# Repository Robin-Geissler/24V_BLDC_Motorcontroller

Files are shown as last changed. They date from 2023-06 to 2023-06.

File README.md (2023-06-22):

# 24V BLDC Motorcontroller

This is a motorcontroller to control a 24V BLDC motor. In this project the controller was used to control a Faulhaber 4221 BXT R to power a 2DOF robot. The 6 Step control algorithm is used to control the motor. The motorcontroller implements the following control modes:
* Current Control
* Speed Control
* Position Control
* Torque Control

## Control Structure
A current controller and a speed controller are used as low level controllers for the position and torque controller. Each controlmode can be accessed by the user.

**Current Control** 
Uses currentsensors on the PCB to control the motor current. 

**Speed Control** 
Calculates the speed by analysing the HAL Sector change rate. 

**Position Control**
The position of the geaboxshaft is measured with an AksIM-2 absolute encoder from RLS. The control structure of the position controller looks like this:
grafik

**Torque Control**
The torque applied to the gearbox shaft is measured with a TS70a torque sensor from ME-Meßsysteme. The control structure of the torque controller looks like this:
grafik

## Comunication Interface
The controller provides an EtherCAT communication interface. Over the interface the controlmode can be set, and PID controlparameters for each controller can be manipulated.

## Hardware
A Microchip ATSAMD51G19A is used as an MCU. It controls a MP6540HA motordriver IC.
grafik

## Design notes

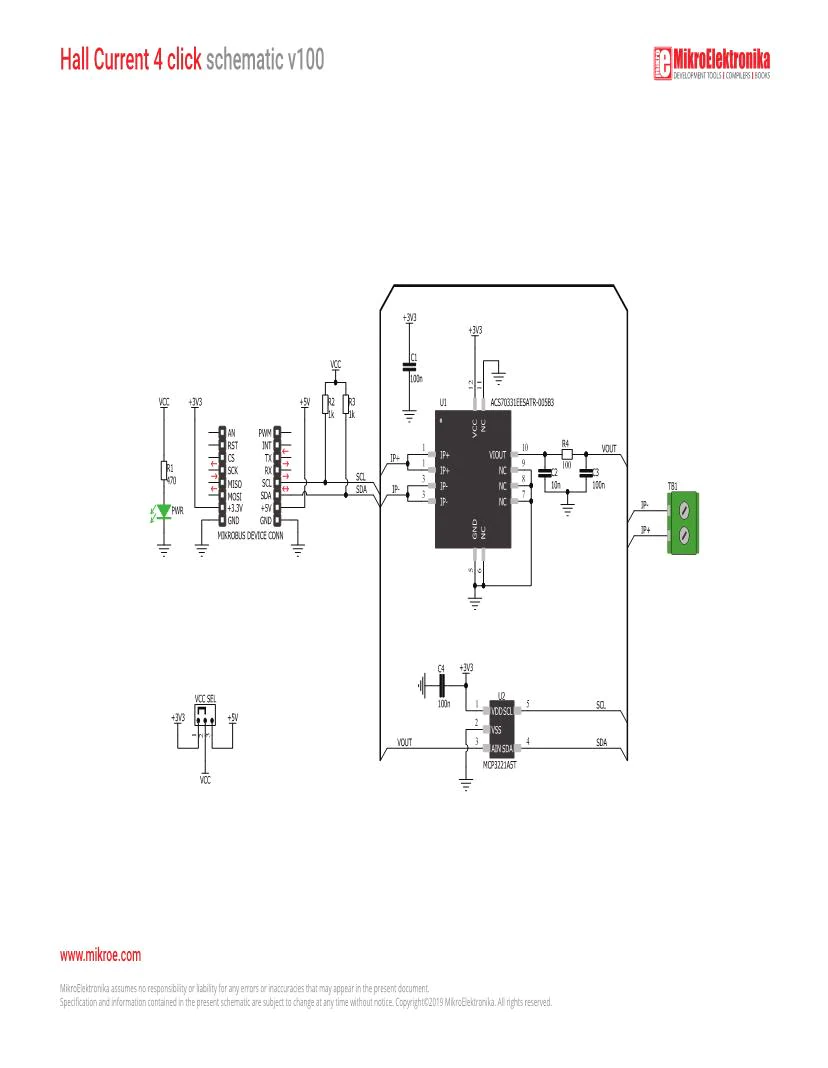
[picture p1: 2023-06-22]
PCB/hall-current-4-click-schematic-v100n-1864020.webp

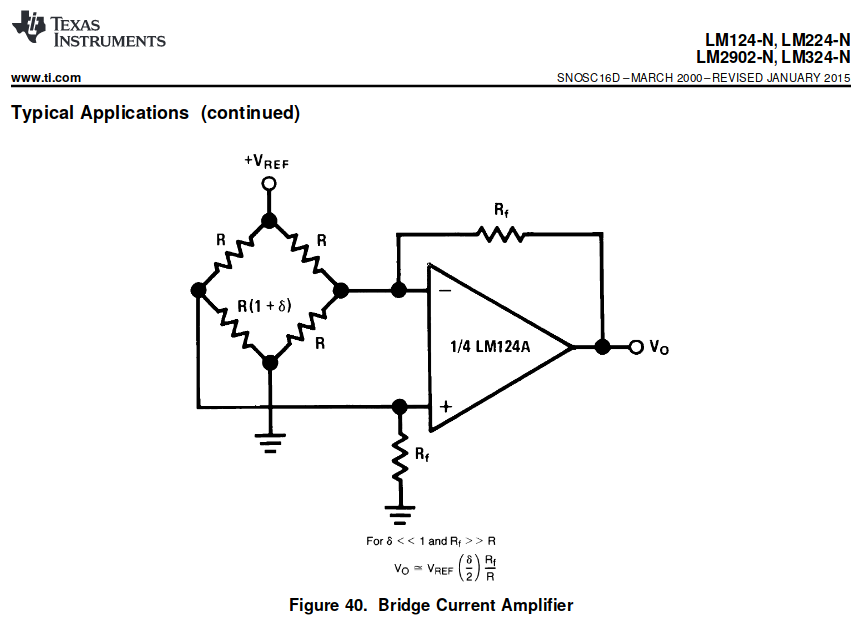
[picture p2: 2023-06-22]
PCB/PZ9ax.png

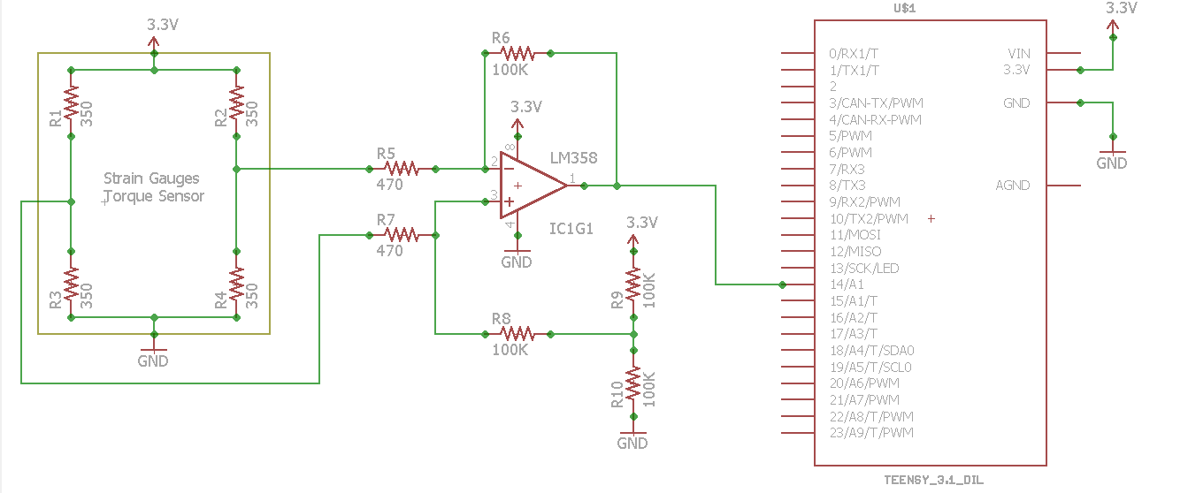
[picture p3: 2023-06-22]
PCB/torquesneosr1.webp

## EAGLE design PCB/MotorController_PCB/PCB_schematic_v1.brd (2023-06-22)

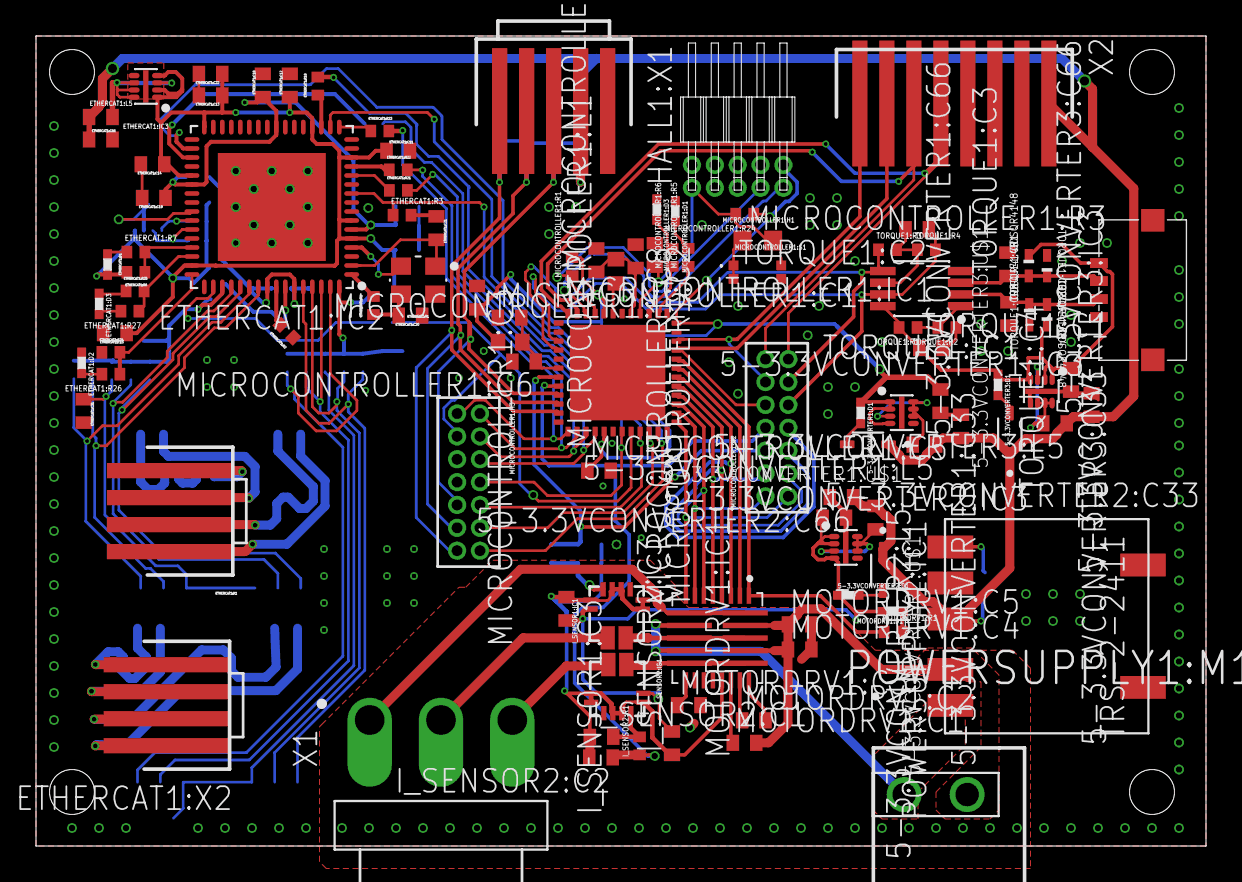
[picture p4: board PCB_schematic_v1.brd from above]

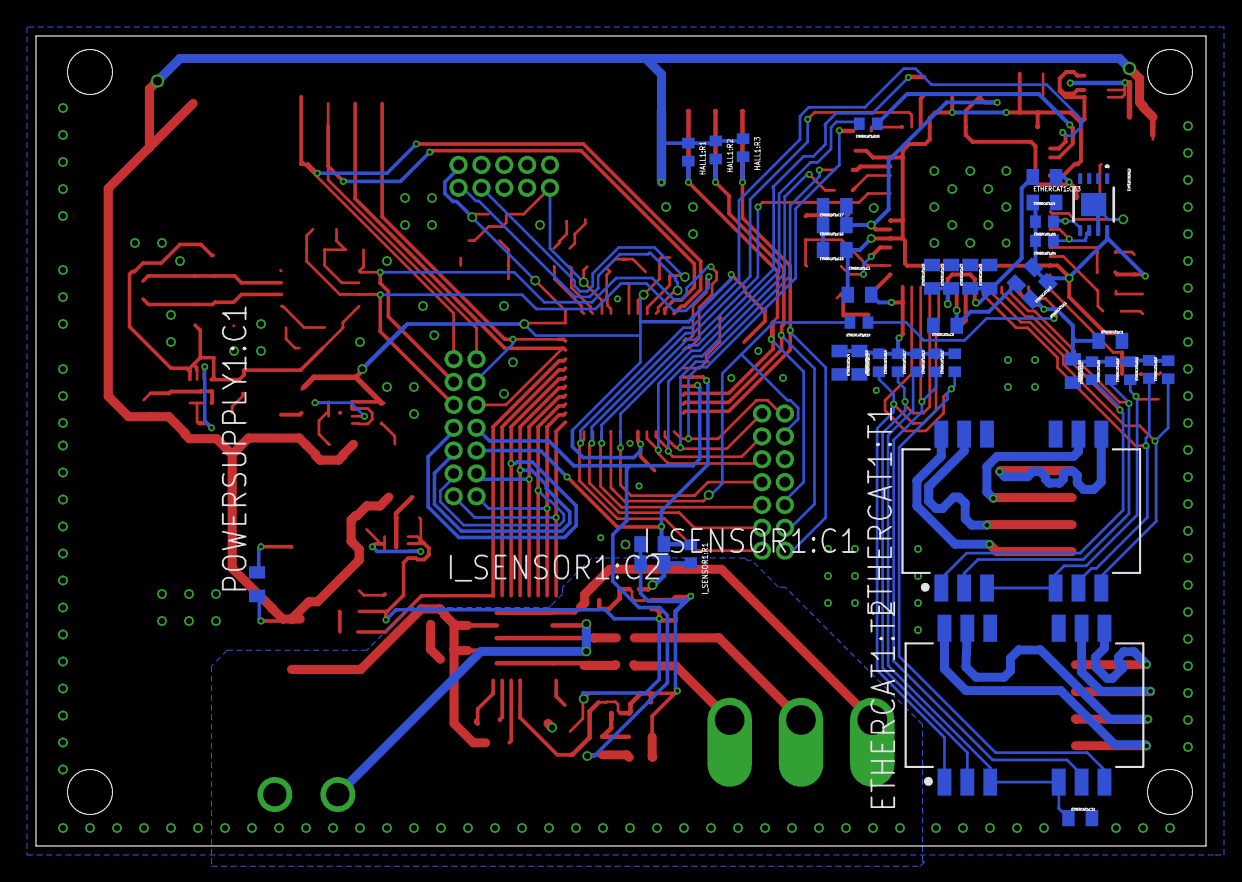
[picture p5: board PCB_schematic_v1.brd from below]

Board: 2 copper layers, 65.0 x 45.0 mm, 150 parts (42 on the bottom side), 111 nets.

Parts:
5-3.3VCONVERTER1:C33, 5-3.3VCONVERTER2:C33, 5-3.3VCONVERTER3:C33: GRM155C80J106ME11D; C0402
5-3.3VCONVERTER1:C66, 5-3.3VCONVERTER2:C66, 5-3.3VCONVERTER3:C66: GCM155C71A105KE38D; C0402
5-3.3VCONVERTER1:D1, 5-3.3VCONVERTER2:D1, 5-3.3VCONVERTER3:D1: QBLP595-R; LED0402
5-3.3VCONVERTER1:IC3, 5-3.3VCONVERTER2:IC3, 5-3.3VCONVERTER3:IC3: RP115L331D-E2; SON40P120X160X40-9T30X130N
5-3.3VCONVERTER1:L5, 5-3.3VCONVERTER2:L5, 5-3.3VCONVERTER3:L5: BLM15EG221SH1D; BEAD0402
5-3.3VCONVERTER1:U$1, 5-3.3VCONVERTER2:U$1, 5-3.3VCONVERTER3:U$1: MM3Z3V0B; SODFL2513X100N
ETHERCAT1:C1, ETHERCAT1:C3, ETHERCAT1:C66: GCM155C71A105KE38D; C0402
ETHERCAT1:C2, ETHERCAT1:C4, ETHERCAT1:C5, ETHERCAT1:C7, ETHERCAT1:C9, ETHERCAT1:C10, ETHERCAT1:C11, ETHERCAT1:C12, ETHERCAT1:C13, ETHERCAT1:C14, ETHERCAT1:C15, ETHERCAT1:C18, ETHERCAT1:C19, ETHERCAT1:C22: 100n; C0402
ETHERCAT1:C6, ETHERCAT1:C8, ETHERCAT1:C16: 1u; C0402
ETHERCAT1:C17: 470p; C0402
ETHERCAT1:C20, ETHERCAT1:C21: 18p; C0402
ETHERCAT1:C31, ETHERCAT1:C32: 22n; C0402
ETHERCAT1:C33: GRM155C80J106ME11D; C0402
ETHERCAT1:D1: QBLP595-IG; LED0402
ETHERCAT1:D2: QBLP595-IB; LED0402
ETHERCAT1:D3: QBLP595-O; LED0402
ETHERCAT1:IC1: CAT24C512IGT3HU5; UDFN8
ETHERCAT1:IC2: LAN9253-I/R4X; QFN64-T600
ETHERCAT1:IC3: RP115L331D-E2; SON40P120X160X40-9T30X130N
ETHERCAT1:L1, ETHERCAT1:L2, ETHERCAT1:L3, ETHERCAT1:L4, ETHERCAT1:L5: BLM15EG221SH1D; BEAD0402
ETHERCAT1:R1, ETHERCAT1:R16, ETHERCAT1:R17: RT0402FRE070RL; R0402
ETHERCAT1:R2: 12k1; R0402
ETHERCAT1:R3, ETHERCAT1:R7, ETHERCAT1:R26, ETHERCAT1:R27: RL1206FR-7WL; R0402
ETHERCAT1:R4, ETHERCAT1:R5: 4k7; R0402
ETHERCAT1:R6, ETHERCAT1:R24, ETHERCAT1:R25: 10k; R0402
ETHERCAT1:R8, ETHERCAT1:R9, ETHERCAT1:R10, ETHERCAT1:R11, ETHERCAT1:R12, ETHERCAT1:R13, ETHERCAT1:R14, ETHERCAT1:R15: 49R9; R0402
ETHERCAT1:R18, ETHERCAT1:R19, ETHERCAT1:R20, ETHERCAT1:R21, ETHERCAT1:R22, ETHERCAT1:R23: 100; R0402
ETHERCAT1:T1, ETHERCAT1:T2: 749020100; SOIC127P965X533-16-TRAFO
ETHERCAT1:X1, ETHERCAT1:X2: 87438-0443; 87438-04
ETHERCAT1:Y1: ECX-2236
HALL1:R1, HALL1:R2, HALL1:R3: RT0402BRD0710KL; R0402
HALL1:X1: 87438-0543; 87438-05
I_SENSOR1:C1, I_SENSOR2:C1: GCM155R71E103KA37; C0402
I_SENSOR1:C2, I_SENSOR1:C3, I_SENSOR2:C2, I_SENSOR2:C3: GCM155R71C104JA55; C0402
I_SENSOR1:IC1, I_SENSOR2:IC1: ACS70331EESATR-005B3; QFN12-ES
I_SENSOR1:R1, I_SENSOR2:R1: RT0402FRE07100RL; R0402
MICROCONTROLLER1:C1, MICROCONTROLLER1:C3: GRM155C80J106ME11D; C0402
MICROCONTROLLER1:C2, MICROCONTROLLER1:C5, MICROCONTROLLER1:C6, MICROCONTROLLER1:C7: GCM155R71C104JA55; C0402
MICROCONTROLLER1:C8: GRM155C80J475MEAAD; C0402
MICROCONTROLLER1:D1, MICROCONTROLLER1:D3: QBLP595-AG; LED0402
MICROCONTROLLER1:H1: 20021112-00010T4LF; 20021112-00010
MICROCONTROLLER1:H2, MICROCONTROLLER1:H3: 20021111-00014T1LF; 20021111-00014
MICROCONTROLLER1:IC1: ATSAMD51G19A-MUT; QFN48
MICROCONTROLLER1:L1, MICROCONTROLLER1:L2: BLM18EG601SN1D; BEADC1608X80
MICROCONTROLLER1:R1: RT0402FRE071KL; R0402
MICROCONTROLLER1:R3: RT0603FRE07330RL; R0603
MICROCONTROLLER1:R5, MICROCONTROLLER1:R6, MICROCONTROLLER1:R24: 10k; R0402
MICROCONTROLLER1:S1: USLPT2616CT2TR; USLPT2616CT
MOTORDRV1:C1: GRM155R6YA105KE11D; C0402
MOTORDRV1:C2, MOTORDRV1:C4, MOTORDRV1:C5: GRM155R62A104KE14; C0402
MOTORDRV1:C3: GRM155R61H472KA01D; C0402
MOTORDRV1:D1: QBLP595-R; LED0402
MOTORDRV1:IC1: MP6540HGUP
MOTORDRV1:R1: RT0402BRD0710KL; R0402
POWERSUPPLY1:C1: GRM155R6YA105KE11D; C0402
POWERSUPPLY1:IC1: TRS-2-2411; 7-SMD
POWERSUPPLY1:M1: PST1,3/2-3,5; 1945096
POWERSUPPLY1:U$1: PTDA1,5/2-PH-3,5; 1725107
TORQUE1:C1: GCM155R71C104JA55; C0402
TORQUE1:C2, TORQUE1:C3, TORQUE1:C4: GCM155R71E103KA37; C0402
TORQUE1:CR1, TORQUE1:CR2, TORQUE1:CR3, TORQUE1:CR4: CDSQR4148; 0402/SOD-923F
TORQUE1:IC1: MAX4208AUA+T; USOP8
TORQUE1:R1, TORQUE1:R2: RT0402FRE0710KL; R0402
TORQUE1:R3: RT0402FRE07150RL; R0402
TORQUE1:R4: RT0402FRE07100KL; R0402
TORQUE1:X3: 5037630491
X1: B3PS-VH(LF)(SN)
X2: 87438-0843; 87438-08

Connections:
5-3.3VCONVERTER1:N$1: 5-3.3VCONVERTER1:D1.2, 5-3.3VCONVERTER1:U$1.A
5-3.3VCONVERTER1:VDD: 5-3.3VCONVERTER1:IC3.3, 5-3.3VCONVERTER1:IC3.6, 5-3.3VCONVERTER1:IC3.7, 5-3.3VCONVERTER1:IC3.8, 5-3.3VCONVERTER1:L5.2
5-3.3VCONVERTER2:N$1: 5-3.3VCONVERTER2:D1.2, 5-3.3VCONVERTER2:U$1.A
5-3.3VCONVERTER2:VDD: 5-3.3VCONVERTER2:IC3.3, 5-3.3VCONVERTER2:IC3.6, 5-3.3VCONVERTER2:IC3.7, 5-3.3VCONVERTER2:IC3.8, 5-3.3VCONVERTER2:L5.2
5-3.3VCONVERTER3:N$1: 5-3.3VCONVERTER3:D1.2, 5-3.3VCONVERTER3:U$1.A
5-3.3VCONVERTER3:VDD: 5-3.3VCONVERTER3:IC3.3, 5-3.3VCONVERTER3:IC3.6, 5-3.3VCONVERTER3:IC3.7, 5-3.3VCONVERTER3:IC3.8, 5-3.3VCONVERTER3:L5.2
+3V3_MD: 5-3.3VCONVERTER2:C33.1, 5-3.3VCONVERTER2:D1.1, 5-3.3VCONVERTER2:IC3.1, 5-3.3VCONVERTER2:IC3.2, 5-3.3VCONVERTER2:IC3.4, I_SENSOR1:C3.2, I_SENSOR1:IC1.12, I_SENSOR2:C3.2, I_SENSOR2:IC1.12, MOTORDRV1:D1.2
+3V3_TS: 5-3.3VCONVERTER3:C33.1, 5-3.3VCONVERTER3:D1.1, 5-3.3VCONVERTER3:IC3.1, 5-3.3VCONVERTER3:IC3.2, 5-3.3VCONVERTER3:IC3.4, TORQUE1:C1.1, TORQUE1:CR1.2, TORQUE1:CR4.2, TORQUE1:IC1.8, TORQUE1:R1.2, TORQUE1:X3.4
+3V3_UC: 5-3.3VCONVERTER1:C33.1, 5-3.3VCONVERTER1:D1.1, 5-3.3VCONVERTER1:IC3.1, 5-3.3VCONVERTER1:IC3.2, 5-3.3VCONVERTER1:IC3.4, MICROCONTROLLER1:C3.2, MICROCONTROLLER1:C5.1, MICROCONTROLLER1:H1.1, MICROCONTROLLER1:IC1.17, MICROCONTROLLER1:IC1.36, MICROCONTROLLER1:IC1.44, MICROCONTROLLER1:L2.1, MICROCONTROLLER1:R1.2, MICROCONTROLLER1:R24.1
+5V: 5-3.3VCONVERTER1:C66.1, 5-3.3VCONVERTER1:L5.1, 5-3.3VCONVERTER1:U$1.C, 5-3.3VCONVERTER2:C66.1, 5-3.3VCONVERTER2:L5.1, 5-3.3VCONVERTER2:U$1.C, 5-3.3VCONVERTER3:C66.1, 5-3.3VCONVERTER3:L5.1, 5-3.3VCONVERTER3:U$1.C, ETHERCAT1:C66.1, ETHERCAT1:L5.1, HALL1:R1.1, HALL1:R2.1, HALL1:R3.1, HALL1:X1.2, POWERSUPPLY1:C1.1, POWERSUPPLY1:IC1.3, X2.1
+24V: MOTORDRV1:C1.2, MOTORDRV1:C4.1, MOTORDRV1:C5.1, MOTORDRV1:IC1.23, MOTORDRV1:IC1.25, POWERSUPPLY1:IC1.2, POWERSUPPLY1:M1.2
ADC_TS: MICROCONTROLLER1:H2.9, MICROCONTROLLER1:IC1.3, TORQUE1:C2.1, TORQUE1:IC1.7, TORQUE1:R4.2
AGND: MOTORDRV1:C3.2, MOTORDRV1:C4.2, MOTORDRV1:C5.2, MOTORDRV1:IC1.10, MOTORDRV1:IC1.12, POWERSUPPLY1:IC1.1, POWERSUPPLY1:M1.1
ENA: MICROCONTROLLER1:H2.7, MICROCONTROLLER1:IC1.30, MOTORDRV1:IC1.3
ENB: MICROCONTROLLER1:H2.5, MICROCONTROLLER1:IC1.29, MOTORDRV1:IC1.4
ENC: MICROCONTROLLER1:H2.4, MICROCONTROLLER1:IC1.28, MOTORDRV1:IC1.5
ENCODER_SPI_MISO: MICROCONTROLLER1:H2.10, MICROCONTROLLER1:IC1.33, X2.7
ENCODER_SPI_MOSI: MICROCONTROLLER1:H2.12, MICROCONTROLLER1:IC1.34, X2.8
ENCODER_SPI_NCS: MICROCONTROLLER1:H2.14, MICROCONTROLLER1:IC1.47, X2.6
ENCODER_SPI_SCK: MICROCONTROLLER1:H2.13, MICROCONTROLLER1:IC1.48, X2.5
ETHERCAT1:#MISO: ETHERCAT1:IC2.13, ETHERCAT1:R22.1
ETHERCAT1:#MOSI: ETHERCAT1:IC2.17, ETHERCAT1:R23.1
ETHERCAT1:#SCK: ETHERCAT1:IC2.19, ETHERCAT1:R18.1
ETHERCAT1:#SCS#: ETHERCAT1:IC2.50, ETHERCAT1:R19.1
ETHERCAT1:#SQI2: ETHERCAT1:IC2.12, ETHERCAT1:R21.1
ETHERCAT1:#SQI3: ETHERCAT1:IC2.35, ETHERCAT1:R20.1
ETHERCAT1:+3V3: ETHERCAT1:C10.1, ETHERCAT1:C11.1, ETHERCAT1:C12.1, ETHERCAT1:C13.1, ETHERCAT1:C14.1, ETHERCAT1:C15.1, ETHERCAT1:C22.1, ETHERCAT1:C33.1, ETHERCAT1:D1.2, ETHERCAT1:IC1.8, ETHERCAT1:IC2.5, ETHERCAT1:IC2.7, ETHERCAT1:IC2.14, ETHERCAT1:IC2.20, ETHERCAT1:IC2.32, ETHERCAT1:IC2.37, ETHERCAT1:IC2.47, ETHERCAT1:IC3.1, ETHERCAT1:IC3.2, ETHERCAT1:IC3.4, ETHERCAT1:L1.1, ETHERCAT1:L2.1, ETHERCAT1:L3.1, ETHERCAT1:R4.2, ETHERCAT1:R5.2, ETHERCAT1:R6.2
ETHERCAT1:CT1: ETHERCAT1:C31.1, ETHERCAT1:R16.1, ETHERCAT1:T1.3, ETHERCAT1:T1.6
ETHERCAT1:CT2: ETHERCAT1:C32.1, ETHERCAT1:R17.1, ETHERCAT1:T2.3, ETHERCAT1:T2.6
ETHERCAT1:GPIO0: ETHERCAT1:IC2.48, ETHERCAT1:R24.2, ETHERCAT1:R26.1
ETHERCAT1:GPIO1: ETHERCAT1:IC2.46, ETHERCAT1:R25.2, ETHERCAT1:R27.1
ETHERCAT1:GPIO2: ETHERCAT1:IC2.45, ETHERCAT1:R6.1, ETHERCAT1:R7.2
ETHERCAT1:I2C_SCL: ETHERCAT1:IC1.6, ETHERCAT1:IC2.43, ETHERCAT1:R4.1
ETHERCAT1:I2C_SDA: ETHERCAT1:IC1.5, ETHERCAT1:IC2.42, ETHERCAT1:R5.1
ETHERCAT1:IN_RX_N: ETHERCAT1:T1.9, ETHERCAT1:X1.4
ETHERCAT1:IN_RX_P: ETHERCAT1:T1.10, ETHERCAT1:X1.3
ETHERCAT1:IN_TX_N: ETHERCAT1:T1.15, ETHERCAT1:X1.2
ETHERCAT1:IN_TX_P: ETHERCAT1:T1.16, ETHERCAT1:X1.1
ETHERCAT1:N$1: ETHERCAT1:D2.2, ETHERCAT1:R26.2
ETHERCAT1:N$2: ETHERCAT1:D3.2, ETHERCAT1:R27.2
ETHERCAT1:N$3: ETHERCAT1:IC3.3, ETHERCAT1:IC3.6, ETHERCAT1:IC3.7, ETHERCAT1:IC3.8, ETHERCAT1:L5.2
ETHERCAT1:N$15: ETHERCAT1:D1.1, ETHERCAT1:R7.1
ETHERCAT1:OSCI: ETHERCAT1:IC2.1, ETHERCAT1:R1.2
ETHERCAT1:OSCI1: ETHERCAT1:C20.2, ETHERCAT1:R1.1, ETHERCAT1:Y1.3
ETHERCAT1:OSCO: ETHERCAT1:C21.2, ETHERCAT1:IC2.2, ETHERCAT1:Y1.1
ETHERCAT1:OUT_RX_N: ETHERCAT1:T2.9, ETHERCAT1:X2.4
ETHERCAT1:OUT_RX_P: ETHERCAT1:T2.10, ETHERCAT1:X2.3
ETHERCAT1:OUT_TX_N: ETHERCAT1:T2.15, ETHERCAT1:X2.2
ETHERCAT1:OUT_TX_P: ETHERCAT1:T2.16, ETHERCAT1:X2.1
ETHERCAT1:RBIAS: ETHERCAT1:IC2.57, ETHERCAT1:R2.2
ETHERCAT1:RXA_N: ETHERCAT1:IC2.54, ETHERCAT1:R10.1, ETHERCAT1:T1.8
ETHERCAT1:RXA_P: ETHERCAT1:IC2.55, ETHERCAT1:R11.1, ETHERCAT1:T1.7
ETHERCAT1:RXB_N: ETHERCAT1:IC2.61, ETHERCAT1:R14.1, ETHERCAT1:T2.2
ETHERCAT1:RXB_P: ETHERCAT1:IC2.60, ETHERCAT1:R15.1, ETHERCAT1:T2.1
ETHERCAT1:TXA_N: ETHERCAT1:IC2.52, ETHERCAT1:R8.1, ETHERCAT1:T1.2
ETHERCAT1:TXA_P: ETHERCAT1:IC2.53, ETHERCAT1:R9.1, ETHERCAT1:T1.1
ETHERCAT1:TXB_N: ETHERCAT1:IC2.63, ETHERCAT1:R12.1, ETHERCAT1:T2.8
ETHERCAT1:TXB_P: ETHERCAT1:IC2.62, ETHERCAT1:R13.1, ETHERCAT1:T2.7
ETHERCAT1:VDD: ETHERCAT1:C16.1, ETHERCAT1:C17.1, ETHERCAT1:C18.1, ETHERCAT1:C19.1, ETHERCAT1:IC2.6, ETHERCAT1:IC2.24, ETHERCAT1:IC2.38, ETHERCAT1:L4.1
ETHERCAT1:VDD12TX: ETHERCAT1:C6.1, ETHERCAT1:C7.1, ETHERCAT1:C8.1, ETHERCAT1:C9.1, ETHERCAT1:IC2.56, ETHERCAT1:IC2.59, ETHERCAT1:L4.2
ETHERCAT1:VDD33BIAS: ETHERCAT1:C5.1, ETHERCAT1:IC2.58, ETHERCAT1:L3.2
ETHERCAT1:VDD33TXRX1: ETHERCAT1:C1.1, ETHERCAT1:C2.1, ETHERCAT1:IC2.51, ETHERCAT1:L1.2, ETHERCAT1:R8.2, ETHERCAT1:R9.2, ETHERCAT1:R10.2, ETHERCAT1:R11.2, ETHERCAT1:R16.2
ETHERCAT1:VDD33TXRX2: ETHERCAT1:C3.1, ETHERCAT1:C4.1, ETHERCAT1:IC2.64, ETHERCAT1:L2.2, ETHERCAT1:R12.2, ETHERCAT1:R13.2, ETHERCAT1:R14.2, ETHERCAT1:R15.2, ETHERCAT1:R17.2
ETH_CS: ETHERCAT1:R19.2, MICROCONTROLLER1:H3.3, MICROCONTROLLER1:IC1.20
ETH_IO2: ETHERCAT1:R21.2, MICROCONTROLLER1:H3.4, MICROCONTROLLER1:IC1.15
ETH_IO3: ETHERCAT1:R20.2, MICROCONTROLLER1:H3.6, MICROCONTROLLER1:IC1.16
ETH_MISO: ETHERCAT1:R22.2, MICROCONTROLLER1:H3.2, MICROCONTROLLER1:IC1.14
ETH_MOSI: ETHERCAT1:R23.2, MICROCONTROLLER1:H3.1, MICROCONTROLLER1:IC1.13
ETH_SCK: ETHERCAT1:R18.2, MICROCONTROLLER1:H3.8, MICROCONTROLLER1:IC1.19
GND: 5-3.3VCONVERTER1:C33.2, 5-3.3VCONVERTER1:C66.2, 5-3.3VCONVERTER1:IC3.5, 5-3.3VCONVERTER1:IC3.9, 5-3.3VCONVERTER2:C33.2, 5-3.3VCONVERTER2:C66.2, 5-3.3VCONVERTER2:IC3.5, 5-3.3VCONVERTER2:IC3.9, 5-3.3VCONVERTER3:C33.2, 5-3.3VCONVERTER3:C66.2, 5-3.3VCONVERTER3:IC3.5, 5-3.3VCONVERTER3:IC3.9, ETHERCAT1:C1.2, ETHERCAT1:C2.2, ETHERCAT1:C3.2, ETHERCAT1:C4.2, ETHERCAT1:C5.2, ETHERCAT1:C6.2, ETHERCAT1:C7.2, ETHERCAT1:C8.2, ETHERCAT1:C9.2, ETHERCAT1:C10.2, ETHERCAT1:C11.2, ETHERCAT1:C12.2, ETHERCAT1:C13.2, ETHERCAT1:C14.2, ETHERCAT1:C15.2, ETHERCAT1:C16.2, ETHERCAT1:C17.2, ETHERCAT1:C18.2, ETHERCAT1:C19.2, ETHERCAT1:C20.1, ETHERCAT1:C21.1, ETHERCAT1:C22.2, ETHERCAT1:C31.2, ETHERCAT1:C32.2, ETHERCAT1:C33.2, ETHERCAT1:C66.2, ETHERCAT1:D2.1, ETHERCAT1:D3.1, ETHERCAT1:IC1.1, ETHERCAT1:IC1.2, ETHERCAT1:IC1.3, ETHERCAT1:IC1.4, ETHERCAT1:IC1.7, ETHERCAT1:IC1.9, ETHERCAT1:IC2.4, ETHERCAT1:IC2.8, ETHERCAT1:IC2.9, ETHERCAT1:IC2.41, ETHERCAT1:IC2.65, ETHERCAT1:IC3.5, ETHERCAT1:IC3.9, ETHERCAT1:R2.1, ETHERCAT1:R3.2, ETHERCAT1:R24.1, ETHERCAT1:R25.1, ETHERCAT1:Y1.2, ETHERCAT1:Y1.4, HALL1:X1.1, I_SENSOR1:C1.1, I_SENSOR1:C2.2, I_SENSOR1:C3.1, I_SENSOR1:IC1.5, I_SENSOR1:IC1.6, I_SENSOR1:IC1.8, I_SENSOR1:IC1.9, I_SENSOR1:IC1.11, I_SENSOR2:C1.1, I_SENSOR2:C2.2, I_SENSOR2:C3.1, I_SENSOR2:IC1.5, I_SENSOR2:IC1.6, I_SENSOR2:IC1.8, I_SENSOR2:IC1.9, I_SENSOR2:IC1.11, MICROCONTROLLER1:C1.1, MICROCONTROLLER1:C2.1, MICROCONTROLLER1:C3.1, MICROCONTROLLER1:C5.2, MICROCONTROLLER1:C6.2, MICROCONTROLLER1:C7.2, MICROCONTROLLER1:C8.1, MICROCONTROLLER1:D1.1, MICROCONTROLLER1:D3.1, MICROCONTROLLER1:H1.3, MICROCONTROLLER1:H1.5, MICROCONTROLLER1:H3.5, MICROCONTROLLER1:H3.7, MICROCONTROLLER1:IC1.5, MICROCONTROLLER1:IC1.18, MICROCONTROLLER1:IC1.35, MICROCONTROLLER1:IC1.42, MICROCONTROLLER1:S1.2, MICROCONTROLLER1:S1.4, MOTORDRV1:IC1.18, POWERSUPPLY1:C1.2, POWERSUPPLY1:IC1.5, TORQUE1:C1.2, TORQUE1:C3.2, TORQUE1:C4.2, TORQUE1:CR2.1, TORQUE1:CR3.1, TORQUE1:IC1.4, TORQUE1:R2.1, TORQUE1:X3.1, X2.2
HALL_A: HALL1:R3.2, HALL1:X1.5, MICROCONTROLLER1:H3.13, MICROCONTROLLER1:IC1.11
HALL_B: HALL1:R2.2, HALL1:X1.4, MICROCONTROLLER1:H3.11, MICROCONTROLLER1:IC1.10
HALL_C: HALL1:R1.2, HALL1:X1.3, MICROCONTROLLER1:H3.9, MICROCONTROLLER1:IC1.9
I2-: I_SENSOR1:C2.1, I_SENSOR1:R1.1, MICROCONTROLLER1:H2.6, MICROCONTROLLER1:IC1.7
I3+: I_SENSOR2:C2.1, I_SENSOR2:R1.1, MICROCONTROLLER1:H2.8, MICROCONTROLLER1:IC1.8
I_SENSOR1:VI: I_SENSOR1:C1.2, I_SENSOR1:IC1.10, I_SENSOR1:R1.2
I_SENSOR2:VI: I_SENSOR2:C1.2, I_SENSOR2:IC1.10, I_SENSOR2:R1.2
MICROCONTROLLER1:LED_PA27: MICROCONTROLLER1:IC1.39, MICROCONTROLLER1:R6.1
MICROCONTROLLER1:LED_PB23: MICROCONTROLLER1:IC1.38, MICROCONTROLLER1:R5.1
MICROCONTROLLER1:N$1: MICROCONTROLLER1:R3.1, MICROCONTROLLER1:S1.1, MICROCONTROLLER1:S1.3
MICROCONTROLLER1:N$2: MICROCONTROLLER1:D3.2, MICROCONTROLLER1:R6.2
MICROCONTROLLER1:N$4: MICROCONTROLLER1:D1.2, MICROCONTROLLER1:R5.2
MICROCONTROLLER1:NRESET: MICROCONTROLLER1:C2.2, MICROCONTROLLER1:H1.10, MICROCONTROLLER1:IC1.40, MICROCONTROLLER1:R3.2, MICROCONTROLLER1:R24.2
MICROCONTROLLER1:SWCLK: MICROCONTROLLER1:H1.4, MICROCONTROLLER1:IC1.45, MICROCONTROLLER1:R1.1
MICROCONTROLLER1:SWDIO: MICROCONTROLLER1:H1.2, MICROCONTROLLER1:IC1.46
MICROCONTROLLER1:VDDANA: MICROCONTROLLER1:C1.2, MICROCONTROLLER1:C6.1, MICROCONTROLLER1:IC1.6, MICROCONTROLLER1:L2.2
MICROCONTROLLER1:VDDCORE: MICROCONTROLLER1:C7.1, MICROCONTROLLER1:C8.2, MICROCONTROLLER1:IC1.41, MICROCONTROLLER1:L1.2
MICROCONTROLLER1:VSW: MICROCONTROLLER1:IC1.43, MICROCONTROLLER1:L1.1
MOTORDRV1:CP1: MOTORDRV1:C2.1, MOTORDRV1:IC1.20
MOTORDRV1:CP2: MOTORDRV1:C2.2, MOTORDRV1:IC1.21
MOTORDRV1:N$1: MOTORDRV1:D1.1, MOTORDRV1:R1.2
MOTORDRV1:VCP: MOTORDRV1:C1.1, MOTORDRV1:IC1.19
MOTORDRV1:VG: MOTORDRV1:C3.1, MOTORDRV1:IC1.14
NFAULT: MICROCONTROLLER1:IC1.32, MOTORDRV1:IC1.1, MOTORDRV1:R1.1
NSLEEP: MICROCONTROLLER1:IC1.31, MOTORDRV1:IC1.2
OUT1: MOTORDRV1:IC1.9, MOTORDRV1:IC1.26, X1.1
OUT2: I_SENSOR1:IC1.1,2, X1.2
OUT3: I_SENSOR2:IC1.3,4, X1.3
PWMA: MICROCONTROLLER1:H2.3, MICROCONTROLLER1:IC1.27, MOTORDRV1:IC1.6
PWMB: MICROCONTROLLER1:H2.2, MICROCONTROLLER1:IC1.26, MOTORDRV1:IC1.7
PWMC: MICROCONTROLLER1:H2.1, MICROCONTROLLER1:IC1.25, MOTORDRV1:IC1.8
SB: I_SENSOR1:IC1.3,4, MOTORDRV1:IC1.11, MOTORDRV1:IC1.24
SC: I_SENSOR2:IC1.1,2, MOTORDRV1:IC1.13, MOTORDRV1:IC1.22
SYNC0: ETHERCAT1:IC2.34, MICROCONTROLLER1:H3.14, MICROCONTROLLER1:IC1.23
SYNC1: ETHERCAT1:IC2.18, MICROCONTROLLER1:H3.12, MICROCONTROLLER1:IC1.22
TORQUE1:+VO_B: TORQUE1:C3.1, TORQUE1:CR1.1, TORQUE1:CR2.2, TORQUE1:IC1.3, TORQUE1:X3.3
TORQUE1:-VO_B: TORQUE1:C4.1, TORQUE1:CR3.2, TORQUE1:CR4.1, TORQUE1:IC1.2, TORQUE1:X3.2
TORQUE1:VI_REF: TORQUE1:IC1.1, TORQUE1:R1.1, TORQUE1:R2.2
TORQUE1:V_FB: TORQUE1:C2.2, TORQUE1:IC1.6, TORQUE1:R3.2, TORQUE1:R4.1
VREF_TS: MICROCONTROLLER1:H2.11, MICROCONTROLLER1:IC1.4, TORQUE1:IC1.5, TORQUE1:R3.1
WAIT_ACK: ETHERCAT1:IC2.10, ETHERCAT1:R3.1, MICROCONTROLLER1:H3.10, MICROCONTROLLER1:IC1.21

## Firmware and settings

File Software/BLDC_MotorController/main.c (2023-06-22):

/************************************************************************/
/* Integrated Software!!!                                               */
/************************************************************************/

/************************************************************************/
/* Important!!!                                                         */
/************************************************************************/
//Timer for speed capture: Waveform is NFRQ!
//Remember to copy relevant ECAT include files!!!


/************************************************************************/
/* Headers                                                              */
/************************************************************************/
#include <atmel_start.h>
#include "BLDC_driver.h"
#include <math.h>
#include "encoder_driver.h"
#include "qspi_ethercat.h"


/************************************************************************/
/* Definitions                                                          */
/************************************************************************/


#define INPUTCTRL_REG_IC 0x1803		//positive mux current pin (PB09), negative mux internal gnd, non diff mode
#define INPUTCTRL_REG_TS 0x0180		//pos mux vout, neg mux vref, diff mode on
#define ADC_TS_OFFSET -7.0f			//minus 80 (-80) in idle position


/************************************************************************/
/* Global Variables                                                     */
/************************************************************************/


/* Current Measurements */
volatile uint16_t ADC_IB_value;
volatile uint16_t ADC_IC_value;
volatile float currentC_value;
volatile float currentB_value;
volatile float current_reference_current_value = 0;
volatile float last_reference_current_value = 0;
volatile uint8_t new_current_value_available_flag = 0;

/* Speed Measurements */
volatile  float current_BLDC_motor_rpm = 0;
volatile uint16_t CC0_value ;
volatile uint16_t CC1_value ;
volatile uint8_t new_speed_value_available_flag = 0;

/* Position Measurements */
volatile float encoder_joint_pos = 0;
unsigned int encoder_joint_warning_bit = 1;
unsigned int encoder_joint_error_bit = 1;
volatile  char encoder_spi_reply[7] = {};
volatile int new_encoder_reading_flag = 1;
volatile int read_encoder_flag = 0;

/*controller values*/
volatile float error_current = 0;
volatile float error_speed = 0;
volatile float error_position = 0;
volatile float control_voltage_output = 0;
volatile float current_control_output[4] = {0};		//Output - prev. Output - prev. error - not used
volatile float speed_control_output[4] = {0};		//Output - prev. Output - prev. error - not used
volatile float position_control_output[4] = {0};		//Output - prev. Output - prev. error - not used

//general
volatile uint16_t input_control_mode;		//turn on/off controller
volatile uint16_t input_control_set;		//select between inputs

//current control
volatile float input_desired_current;		//target current
volatile float input_max_current;			//max possible current
volatile float input_min_current;			//max negative current
volatile float input_kp_current;			//p gain current control
volatile float input_ki_current;			//i gain current control

//speed control
volatile float input_desired_speed;			//target speed
volatile float input_speed_max;		//max possible motor speed
volatile float input_speed_min;		//max negative motor speed
volatile float input_kp_speed_control;		//p gain position control
volatile float input_ki_speed_control;		//p gain position control

//position control
volatile float input_desired_position;		//target position
 volatile float input_max_position;			// max position
 volatile float input_min_position;			// max neg. position
 volatile float input_kp_position_control;	//p gain position control
 volatile float input_ki_position_control;

//feedforward voltage control
 volatile float input_kt_feedforward = 0;



// ETHERCAT Timer Task
static struct timer_task TIMER_2_task_1kHz;



//Torque sensor
volatile int16_t ADC_TS_value;
volatile float joint_torque = 0.0;
volatile int new_torque_value_available_flag = 0;





/*Controller variables*/
volatile uint8_t activate_controller_flag = 0;








/************************************************************************/
/* Interrupt Service Routines                                           */
/************************************************************************/
/*ISR for speed measurement*/
void TC0_Handler() 
{
	
	if (TC0->COUNT16.INTFLAG.bit.MC0)
	{
		//read results of capture
		CC0_value = TC0->COUNT16.CC[0].reg;
		CC1_value = TC0->COUNT16.CC[1].reg;
		
		TC0->COUNT16.INTFLAG.bit.MC0 = 1;
		TC0->COUNT16.INTFLAG.bit.MC1 = 1;
	} else if (TC0->COUNT16.INTFLAG.bit.OVF){
		//If overflow, motor is not moving
		TC0->COUNT16.INTFLAG.bit.OVF = 1;
		CC0_value = TC0->COUNT16.CC[0].reg;
		CC1_value = TC0->COUNT16.CC[1].reg;
		CC0_value  = 0xFFFF;
	}
	
	//activate encoder
	read_encoder_flag = 1;
	
	//Flag for speed calculation
	new_speed_value_available_flag = 1;

	//clear error bit if any
	hri_tc_clear_INTFLAG_ERR_bit(TC0);
}

/*ISR for current measurement*/
void ADC0_1_Handler()
{
	//either only read TS, or both current sensors in parallel. Reading mode interchange every cycle
	if(ADC0->INPUTCTRL.reg == INPUTCTRL_REG_TS)
	{		
		ADC_TS_value = hri_adc_read_RESULT_reg(ADC0);
		
		//change ADC0 input control to current reading mode
		ADC0->INPUTCTRL.reg = INPUTCTRL_REG_IC;
		
		//Flush results reg 
		ADC0->SWTRIG.bit.FLUSH = 1;
		while (ADC0->SYNCBUSY.bit.SWTRIG == 1){}
			
		//set new torque flag
		new_torque_value_available_flag = 1;
	}
	else
	{
		ADC_IC_value = hri_adc_read_RESULT_reg(ADC0);
		ADC_IB_value = hri_adc_read_RESULT_reg(ADC1);
		
		//change ADC1 input control to torque sensor reading mode
		ADC0->INPUTCTRL.reg = INPUTCTRL_REG_TS;
		
		//Flush results reg 
		ADC0->SWTRIG.bit.FLUSH = 1;
		while (ADC1->SYNCBUSY.bit.SWTRIG == 1){}
			
		//Set new current flag
		new_current_value_available_flag = 1;
	}

	//clear interrupt flag
	hri_adc_clear_INTFLAG_reg(ADC0, 0xFF);
	hri_adc_clear_INTFLAG_reg(ADC1, 0xFF);
	
}


/*Dummy ADC1_1 Handler so that it shuts up ;)*/
void ADC1_1_Handler()
{
}

/*Callback function for Encoder SPI*/
static void complete_cb_SPI_ENC(const struct spi_m_async_descriptor *const io_descr)
{
	//New reading flag
	new_encoder_reading_flag = 1;
	
	//convert received value to angles between 0 and 110 degrees
	conversion_joint_encoder(encoder_spi_reply, &encoder_joint_pos, &encoder_joint_warning_bit, &encoder_joint_error_bit);
	
	//Pull NCS high to stop reading cycle
	delay_us(10); //can be removed
	gpio_set_pin_level(ENCODER_SPI_NCS, true);
}

/*Callback function for EtherCAT QSPI */
static void TIMER_2_task_1kHz_cb(const struct timer_task *const timer_task)
{
  	write_16_DWORDS_data();
  	config_fifo();
  	read_16_DWORDS_data();
	gpio_toggle_pin_level(STATUS_LED1);
	
	//clear_rdram();
}

/************************************************************************/
/* Subfunctions                                                        */
/************************************************************************/
float current_selector(uint32_t current_commutation_state)
{
	switch(current_commutation_state)
	{
		case 5:
			return (-currentC_value);
			break;
		
		case 3:
			return (currentC_value);
			break;
		
		case 4:
			return (-currentB_value);
			break;
		
		case 1:
			return (currentB_value);
			break;
		
		case 0:
			return (currentB_value);
			break;
		
		case 2:
			return (currentC_value);
			break;
			
		default:
			return 0;
	}
}


/************************************************************************/
/* Main Function                                                        */
/************************************************************************/
int main(void){
	/* Initializes MCU, drivers and middleware */
	atmel_start_init();	

	/*enable CCL*/
	CCL->CTRL.bit.ENABLE = 1;
	
	/*set TCC1 CC0 to overwrite all WO/x*/
	TCC1->CTRLA.bit.ENABLE = 0;
	TCC1->WEXCTRL.bit.OTMX = 0x2;
	TCC1->CTRLA.bit.ENABLE = 1;
	
	
	/*ADC Configurations*/
	//Disable ADC Freerun
	ADC0->CTRLB.bit.FREERUN = 0;
	ADC1->CTRLB.bit.FREERUN = 0;
	
	//Initialize ADC0 for current A sensing
	ADC0->INPUTCTRL.reg = INPUTCTRL_REG_IC;
	
	//configure ADC interrupt
	ADC0->INTENSET.bit.RESRDY = 1;
	ADC0->EVCTRL.bit.RESRDYEO = 1;
	ADC0->CTRLA.bit.ENABLE = 1;
//	ADC1->INTENSET.bit.RESRDY = 1;
	ADC1->EVCTRL.bit.RESRDYEO = 1;
	ADC1->CTRLA.bit.ENABLE = 1;

	init_PWM();
	init_currentPID();
	init_speedPID();
	init_posPID();
	init_torquePID();
	
	/*set Motor driver NSLEEP pin*/
	gpio_set_pin_level(NSLEEP, true);
	gpio_set_pin_direction(NSLEEP, GPIO_DIRECTION_OUT);
	
	/*Nested Vector Interrupt settings*/
	__NVIC_EnableIRQ(TC0_IRQn);        
	__NVIC_SetPriority(ADC0_1_IRQn,3);
	__NVIC_EnableIRQ(ADC0_1_IRQn);
	__NVIC_SetPriority(ADC1_1_IRQn,3);
	__NVIC_EnableIRQ(ADC1_1_IRQn);
	
	__enable_irq();
	
	
	///*configure ADC interrupt*/
	//hri_adc_write_INTEN_RESRDY_bit(ADC0,1);
	//adc_async_enable_channel(&ADC_IB, 0);
	////hri_adc_write_INTEN_RESRDY_bit(ADC1,1);
	//adc_async_enable_channel(&ADC_IC, 0);

	////Trigger ADC first conversion
	//ADC0->SWTRIG.bit.START = 1;
	//ADC1->SWTRIG.bit.START = 1;
	
	/*Init UART for comp debug interface*/
// 	struct io_descriptor *io_comp;
// 	usart_sync_get_io_descriptor(&USART_COM, &io_comp);
// 	usart_sync_enable(&USART_COM);
	
	/*Init SPI for Joint encoder*/
	struct io_descriptor *io_enc_spi;
	spi_m_async_get_io_descriptor(&SPI_ENC, &io_enc_spi);
	spi_m_async_register_callback(&SPI_ENC, SPI_M_ASYNC_CB_XFER, (FUNC_PTR)complete_cb_SPI_ENC);
	spi_m_async_enable(&SPI_ENC);
	gpio_set_pin_level(ENCODER_SPI_NCS, true);
	
	
	/*ETHERCAT NEW*/
	init_standard_messages();
	
	qspi_sync_enable(&QUAD_SPI_0);
	delay_ms(25);
	//initialize ethercat register
	abort_fifo();
	clear_rdram();
	
	/* Set up task with 1kHz repetition */
	TIMER_2_task_1kHz.interval = 1;	// every millisecond
	TIMER_2_task_1kHz.cb       = TIMER_2_task_1kHz_cb;
	TIMER_2_task_1kHz.mode     = TIMER_TASK_REPEAT;

	timer_add_task(&TIMER_2, &TIMER_2_task_1kHz);
	timer_start(&TIMER_2);
	
	
	/*ETHERCAT*/
// 	configure_ethercat_dma_descriptors();
// 	__NVIC_EnableIRQ(TC7_IRQn);
// 	__NVIC_EnableIRQ(DMAC_0_IRQn);

	volatile uint8_t  *status				=&send_data[0];
	volatile uint8_t  *run_mode			=(((uint8_t *)&send_data[0])+1);
	volatile uint16_t   *read_hall_sector	=(((uint16_t*)&send_data[0])+1);
	volatile float *read_position			=&send_data[1];
	volatile float  *read_speed		=&send_data[2];
	volatile float  *read_torque 	=&send_data[3]; //float
	volatile float *read_current_i_d		=&send_data[4];
	volatile float  *read_current_i_B		=&send_data[5];
	volatile float  *read_current_i_C			=&send_data[6];
	volatile float  *read_emergency			=&send_data[7];
	volatile float  *read_remain_1		=&send_data[8];
	volatile float  *read_duty_cycle		=&send_data[9];
	volatile float  *read_abs_duty_cycle		=&send_data[10];
	volatile float  *read_remain2		=&send_data[11];
	volatile float  *read_remain3				=&send_data[12];
	volatile float  *read_remain4				=&send_data[13];
	volatile float  *read_remain5				=&send_data[14];
	volatile float  *read_remain6				=&send_data[15];
	
	//read
	volatile	uint16_t *control_mode			=&read_data[0];
	volatile	uint16_t *control_set			=(((uint16_t *)&read_data[0])+1);
	volatile	float *desired_position			=&read_data[1];
	volatile	float *desired_torque			=&read_data[2];
	volatile	float *desired_speed			=&read_data[3];
	volatile	float *I_desired				=&read_data[4];
	volatile	float *speed_max				=&read_data[5];
	volatile	float *I_max					=&read_data[6];
	volatile	float *pos_kp					=&read_data[7];
	volatile	float *pos_ki					=&read_data[8];
	volatile    float *torque_kp			    =&read_data[9];
	volatile	float *torque_ki				=&read_data[10];
	volatile	float *speed_kp					=&read_data[11];
	volatile	float *speed_ki					=&read_data[12];
	volatile	float *i_kp						=&read_data[13];
	volatile	float *i_ki						=&read_data[14];
	volatile	float *remain					=&read_data[15];		
	

	
	/**** 
		Set PWM DUTY CYCLE to 0 for testing
	****/
	set_PWM_dutycycle(20);
	
	/*Main while loop*/
	while (1) {		
		
		
		/************************************************************************/
		/* Encoder Read                                                         */
		/************************************************************************/
		if(read_encoder_flag == 1 && new_encoder_reading_flag == 1)
		{
			//reset flags
			new_encoder_reading_flag = 0;
			read_encoder_flag = 0;
			
			//Print joint position on data visualization
			//print_encoder_joint_data(io_comp, &encoder_joint_pos,  &encoder_joint_warning_bit, &encoder_joint_error_bit);
			
			//pull chip select low for next read
			gpio_set_pin_level(ENCODER_SPI_NCS, false);	
			delay_us(10);
			
			//restart reading
			io_read(io_enc_spi,encoder_spi_reply,7);
		}


		/************************************************************************/
		/*Torque sensor value conversion                                        */
		/************************************************************************/
		if(new_torque_value_available_flag == 1)
		{
			//reset flag
			new_torque_value_available_flag = 0;
			
			joint_torque = (ADC_TS_value + ADC_TS_OFFSET)*1.7*3030.3/708/2048; //max at 12bit/2, 2164.5 from 5Nm/2.31mV for 5 Nm at 3.3V input, 708 Gain of Amplifier Circuit
			
		}
		
		
		/************************************************************************/
		/* Current calculation (RMBM TO CALIBRATE!)                             */
		/************************************************************************/
		if(new_current_value_available_flag == 1)
		{	
			currentC_value = ((ADC_IC_value-1870)*3.3/4096)*10/4;; //offset
			currentB_value = -((ADC_IB_value-1870)*3.3/4096)*10/4; //sensor is installed opposite!
			
			//reset flags
			new_current_value_available_flag = 0;
			activate_controller_flag = 1;
		}
		
		/************************************************************************/
		/* Speed calculation                                                    */
		/************************************************************************/
		/*calculate speed if flag is set*/
		if(new_speed_value_available_flag == 1)
		{
			if(CC0_value == 0xFFFF)
			{
				current_BLDC_motor_rpm  = 0; 
			}
			else 
			{
				current_BLDC_motor_rpm = 60*(12e6/(float)CC0_value)/42;
			}

			//direction opposite to current. Thats why minus
			current_BLDC_motor_rpm = -current_BLDC_motor_rpm * ((float)get_BLDC_direction());
			
			//reset flags
			new_speed_value_available_flag = 0;

		}
		
		
		/*Select reference current*/
		current_reference_current_value = current_selector(get_BLDC_commutation_state());


		/************************************************************************/
		/* Ethercat Pointers                                                    */
		/************************************************************************/
		//Output
		*read_hall_sector = get_BLDC_commutation_state();
		*read_position = encoder_joint_pos;
		*read_speed = current_BLDC_motor_rpm;
		*read_current_i_C = currentC_value;
		*read_current_i_B = currentB_value;
		*read_current_i_d = current_reference_current_value;
		*read_torque = joint_torque;
		*read_duty_cycle = control_voltage_output;
		*read_abs_duty_cycle = control_voltage_output;

		//Input
		input_control_mode = *control_mode;
		input_control_set = *control_set;
		currentPIDControl.desired = *I_desired;
		currentPIDControl.max = MAX_PWM;
		currentPIDControl.min = MIN_PWM;
		currentPIDControl.Kp = *i_kp;
		currentPIDControl.Ki = *i_ki;
		speedPIDControl.desired = *desired_speed;
		speedPIDControl.max = *I_max;
		speedPIDControl.min = -(*I_max);
		speedPIDControl.Kp = *speed_kp;
		speedPIDControl.Ki = *speed_ki;
		posPIDControl.desired = *desired_position;
		posPIDControl.max = *speed_max;
		posPIDControl.min = -(*speed_max);
		posPIDControl.Kp = *pos_kp;
		posPIDControl.Ki = *pos_ki;
		torquePIDControl.desired = *desired_torque;
		torquePIDControl.max = *I_max;
		torquePIDControl.min = -(*I_max);
		torquePIDControl.Kp = *torque_kp;
		torquePIDControl.Ki = *torque_ki;
		
		
		//Overwrites
// 		input_control_mode = 1;
// 		input_control_set = 2;
// 		input_kp_current = 1;
// 		input_ki_current = 1100;
// 		input_desired_current = 0.1;	
// 		input_max_current = 0.5;
// 		input_min_current = -input_max_current;
// 		input_kp_speed_control = 0.001;
// 		input_ki_speed_control = 0.03;
// 		input_kp_position_control = 200;
// 		input_ki_position_control = 0;
// 		input_kt_feedforward = 1/997; //inverse of speed constant from datasheet
// 		input_kt_feedforward = 0;
// 		input_desired_speed = 50;
// 		input_desired_position = 1000;
// 		input_speed_max = 1000;
		
/*		input_kp_position_control = *pos_kp;*/		
				
		
		
		/************************************************************************/
		/* Active Driver                                               */
		/************************************************************************/
 		if(activate_controller_flag == 1 && input_control_mode == 1)
 		{
 			/* reset control routine activation flag */
 			activate_controller_flag = 0;
 			
			 /* use control algorithm */
 			switch(input_control_set){
				case CONTROL_SET_CURRENT: BLDC_control_current();
				break;
				case CONTROL_SET_SPEED: BLDC_control_speed();
				break;
				case CONTROL_SET_POSITION: BLDC_control_position();
				break;
				case CONTROL_SET_TORQUE: BLDC_control_torque();
				break;
				default:
				control_voltage_output = 0;
			 }
			
			/*Drive the motor*/
			BLDC_drive(control_voltage_output);
		}
		/************************************************************************/
		/* Non-Active Driver										*/
		/************************************************************************/
		else
		{
			BLDC_drive(0);
		}

		/*Drive BLDC if to bypass controller*/
		//BLDC_drive(5);
 	}
}

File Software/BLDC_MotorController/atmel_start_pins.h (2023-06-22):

/*
 * Code generated from Atmel Start.
 *
 * This file will be overwritten when reconfiguring your Atmel Start project.
 * Please copy examples or other code you want to keep to a separate file
 * to avoid losing it when reconfiguring.
 */
#ifndef ATMEL_START_PINS_H_INCLUDED
#define ATMEL_START_PINS_H_INCLUDED

#include <hal_gpio.h>

// SAMD51 has 14 pin functions

#define GPIO_PIN_FUNCTION_A 0
#define GPIO_PIN_FUNCTION_B 1
#define GPIO_PIN_FUNCTION_C 2
#define GPIO_PIN_FUNCTION_D 3
#define GPIO_PIN_FUNCTION_E 4
#define GPIO_PIN_FUNCTION_F 5
#define GPIO_PIN_FUNCTION_G 6
#define GPIO_PIN_FUNCTION_H 7
#define GPIO_PIN_FUNCTION_I 8
#define GPIO_PIN_FUNCTION_J 9
#define GPIO_PIN_FUNCTION_K 10
#define GPIO_PIN_FUNCTION_L 11
#define GPIO_PIN_FUNCTION_M 12
#define GPIO_PIN_FUNCTION_N 13

#define ADC_PLUS GPIO(GPIO_PORTA, 2)
#define ADC_MINUS GPIO(GPIO_PORTA, 3)
#define HALL_C GPIO(GPIO_PORTA, 4)
#define HALL_B GPIO(GPIO_PORTA, 5)
#define HALL_A GPIO(GPIO_PORTA, 6)
#define HALL_OUT GPIO(GPIO_PORTA, 7)
#define ECAT_SPI_DATA0 GPIO(GPIO_PORTA, 8)
#define ECAT_SPI_DATA1 GPIO(GPIO_PORTA, 9)
#define ECAT_SPI_DATA2 GPIO(GPIO_PORTA, 10)
#define ECAT_SPI_DATA3 GPIO(GPIO_PORTA, 11)
#define ECAT_GPIO1 GPIO(GPIO_PORTA, 12)
#define ECAT_GPIO2 GPIO(GPIO_PORTA, 13)
#define ECAT_GPIO3 GPIO(GPIO_PORTA, 14)
#define ECAT_GPIO4 GPIO(GPIO_PORTA, 15)
#define PWM_C GPIO(GPIO_PORTA, 16)
#define PWM_B GPIO(GPIO_PORTA, 17)
#define PWM_A GPIO(GPIO_PORTA, 18)
#define EN_C GPIO(GPIO_PORTA, 19)
#define EN_B GPIO(GPIO_PORTA, 20)
#define EN_A GPIO(GPIO_PORTA, 21)
#define NSLEEP GPIO(GPIO_PORTA, 22)
#define NFAULT GPIO(GPIO_PORTA, 23)
#define ENCODER_SPI_MISO GPIO(GPIO_PORTA, 24)
#define ENCODER_SPI_MOSI GPIO(GPIO_PORTA, 25)
#define STATUS_LED1 GPIO(GPIO_PORTA, 27)
#define ENCODER_SPI_NCS GPIO(GPIO_PORTB, 2)
#define ENCODER_SPI_SCK GPIO(GPIO_PORTB, 3)
#define ADC_A GPIO(GPIO_PORTB, 8)
#define ADC_B GPIO(GPIO_PORTB, 9)
#define ECAT_SPI_SCK GPIO(GPIO_PORTB, 10)
#define ECAT_SPI_CS GPIO(GPIO_PORTB, 11)
#define STATUS_LED2 GPIO(GPIO_PORTB, 23)

#endif // ATMEL_START_PINS_H_INCLUDED

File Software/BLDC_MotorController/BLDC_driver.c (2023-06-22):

/*
 * BLDC_driver.c
 *
 * Created: 26/11/2022 14:42:10
 *  
 */ 

#include "BLDC_driver.h"
#include "BLDC_Control_Law.h"


/************************************************************************/
/* Init Functions													*/
/************************************************************************/
void init_PWM(){
	hri_tcc_write_CTRLA_ENABLE_bit(TCC1, 0 << TCC_CTRLA_ENABLE_Pos); /* Enable: disabled */
	hri_tcc_write_WAVE_reg(TCC1,
	1 << TCC_WAVE_SWAP3_Pos         /* Swap DTI Output Pair 3: disabled */
	| 0 << TCC_WAVE_SWAP2_Pos   /* Swap DTI Output Pair 2: disabled */
	| 0 << TCC_WAVE_SWAP1_Pos   /* Swap DTI Output Pair 1: disabled */
	| 0 << TCC_WAVE_SWAP0_Pos   /* Swap DTI Output Pair 0: disabled */
	| 0 << TCC_WAVE_CICCEN3_Pos /*  Circular Channel 3 Enable: disabled */
	| 0 << TCC_WAVE_CICCEN2_Pos /*  Circular Channel 2 Enable: disabled */
	| 0 << TCC_WAVE_CICCEN1_Pos /*  Circular Channel 1 Enable: disabled */
	| 0 << TCC_WAVE_CICCEN0_Pos /*  Circular Channel 0 Enable: disabled */
	| 0 << TCC_WAVE_POL5_Pos    /* Channel 5 Polarity: disabled */
	| 0 << TCC_WAVE_POL4_Pos    /* Channel 4 Polarity: disabled */
	| 0 << TCC_WAVE_POL3_Pos    /* Channel 3 Polarity: disabled */
	| 0 << TCC_WAVE_POL2_Pos    /* Channel 2 Polarity: disabled */
	| 0 << TCC_WAVE_POL1_Pos    /* Channel 1 Polarity: disabled */
	| 0 << TCC_WAVE_POL0_Pos    /* Channel 0 Polarity: disabled */
	| 0 << TCC_WAVE_CIPEREN_Pos /* Circular period Enable: disabled */
	| 0 << TCC_WAVE_RAMP_Pos    /* Ramp Mode: 0 */
	| 5);                       /* Waveform Generation: 2 */
	hri_tcc_write_WEXCTRL_OTMX_bf(TCC1, 2);
	hri_tcc_write_WEXCTRL_DTHS_bf(TCC1, 30);
	hri_tcc_write_WEXCTRL_DTLS_bf(TCC1, 30);
	hri_tcc_write_WEXCTRL_DTIEN0_bit(TCC1, 1);
	hri_tcc_write_WEXCTRL_DTIEN1_bit(TCC1, 1);
	hri_tcc_write_WEXCTRL_DTIEN2_bit(TCC1, 1);
	hri_tcc_write_WEXCTRL_DTIEN3_bit(TCC1, 1);
	hri_tcc_write_CTRLA_ENABLE_bit(TCC1, 1 << TCC_CTRLA_ENABLE_Pos); /* Enable: enabled */
}

/************************************************************************/
/* BLDC Subfunctions													*/
/************************************************************************/
/*set the PWM dutycycle to a value between 0 and 100. Return -1 if DC is invalid and 0 if ok*/
int set_PWM_dutycycle(float dutycycle)
{
	if(dutycycle>100)
	{
		dutycycle = 100;
	}
	
	if(dutycycle>=0 && dutycycle<=100)
	{	
		hri_tcc_write_CCBUF_reg(TCC1, 0, (uint16_t)((PWM_25KHZ_PERIOD - (dutycycle*PWM_25KHZ_PERIOD)/100)));
	}
	else
	{
		return -1;
	}
	
	return 0;
}

void init_currentPID(){
	currentPIDControl.desired = 0;
	currentPIDControl.Kp = 0;
	currentPIDControl.Ki = 0;
	currentPIDControl.Kd = 0;
	currentPIDControl.N = 0;
	currentPIDControl.max = 0;
	currentPIDControl.min = 0;
	currentPIDVar.y_k[0] = 0.0;
	currentPIDVar.y_k[1] = 0.0;
	currentPIDVar.y_k[2] = 0.0;
	currentPIDVar.e_k[0] = 0.0;
	currentPIDVar.e_k[1] = 0.0;
	currentPIDVar.e_k[2] = 0.0;
	currentPIDVar.d_y[0] = 0.0;
	currentPIDVar.d_y[1] = 0.0;
	currentPIDVar.d_y[2] = 0.0;
	
}

void init_speedPID(){
	speedPIDControl.desired = 0;
	speedPIDControl.Kp = 0;
	speedPIDControl.Ki = 0;
	speedPIDControl.Kd = 0;
	speedPIDControl.N = 0;
	speedPIDControl.max = 0;
	speedPIDControl.min = 0;
	speedPIDVar.y_k[0] = 0.0;
	speedPIDVar.y_k[1] = 0.0;
	speedPIDVar.y_k[2] = 0.0;
	speedPIDVar.e_k[0] = 0.0;
	speedPIDVar.e_k[1] = 0.0;
	speedPIDVar.e_k[2] = 0.0;
	speedPIDVar.d_y[0] = 0.0;
	speedPIDVar.d_y[1] = 0.0;
	speedPIDVar.d_y[2] = 0.0;
}

void init_posPID(){
	posPIDControl.desired = 0;
	posPIDControl.Kp = 0;
	posPIDControl.Ki = 0;
	posPIDControl.Kd = 0;
	posPIDControl.N = 0;
	posPIDControl.max = 0;
	posPIDControl.min = 0;
	posPIDVar.y_k[0] = 0.0;
	posPIDVar.y_k[1] = 0.0;
	posPIDVar.y_k[2] = 0.0;
	posPIDVar.e_k[0] = 0.0;
	posPIDVar.e_k[1] = 0.0;
	posPIDVar.e_k[2] = 0.0;
	posPIDVar.d_y[0] = 0.0;
	posPIDVar.d_y[1] = 0.0;
	posPIDVar.d_y[2] = 0.0;
}

void init_torquePID(){
	torquePIDControl.desired = 0;
	torquePIDControl.Kp = 0;
	torquePIDControl.Ki = 0;
	torquePIDControl.Kd = 0;
	torquePIDControl.N = 0;
	torquePIDControl.max = 0;
	torquePIDControl.min = 0;
	torquePIDVar.y_k[0] = 0.0;
	torquePIDVar.y_k[1] = 0.0;
	torquePIDVar.y_k[2] = 0.0;
	torquePIDVar.e_k[0] = 0.0;
	torquePIDVar.e_k[1] = 0.0;
	torquePIDVar.e_k[2] = 0.0;
	torquePIDVar.d_y[0] = 0.0;
	torquePIDVar.d_y[1] = 0.0;
	torquePIDVar.d_y[2] = 0.0;
}


/*Read Hallsensor values and find the current commutation state*/
void BLDC_find_step()
{
	last_BLDC_commutation_state = current_BLDC_commutation_state;
	
	uint32_t portlevel = (0x0070 & gpio_get_port_level(0)) >> 4;		
	switch(portlevel)
	{
		/* 110 */ 
		case 6:
			current_BLDC_commutation_state = 0;
			break;
		/* 010 */ 	
		case 2:
			current_BLDC_commutation_state = 1;
			break;
		/* 011 */
		case 3:
			current_BLDC_commutation_state = 2;
			break;
		/* 001 */	
		case 1:
			current_BLDC_commutation_state = 3;
			break;
		/* 101 */	
		case 5:
			current_BLDC_commutation_state = 4;
			break;
		/* 100 */	
		case 4:
			current_BLDC_commutation_state = 5;
			break;
			
		default:
			current_BLDC_commutation_state = -1;
	}
}

void boundary_Check(float *input, float max, float min){
	if(*input > max)
 	{
 		*input = max;
 	} else if (*input < min){
		*input = min;
	}
}


/*Calculate BLDC revolutions*/
void BLDC_revolution_counter()
{
	if (current_BLDC_commutation_state==5 && last_BLDC_commutation_state==0)
	{
		BLDC_revolutions--;
	}
	else if(current_BLDC_commutation_state==0 && last_BLDC_commutation_state==5)
	{
		BLDC_revolutions++;
	}
	
	BLDC_relative_steps = BLDC_revolutions*6.0 + current_BLDC_commutation_state;
}
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

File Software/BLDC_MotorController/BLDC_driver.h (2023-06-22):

/*
 * BLDC_driver.h
 *
 * Created: 26/11/2022 14:41:58
 *  
 */ 


#ifndef BLDC_DRIVER_H_
#define BLDC_DRIVER_H_

#include <atmel_start.h>
#include "BLDC_Control_Law.h"

#define PWM_25KHZ_PERIOD 0x7d2
//#define DUTYCYCLE_05_PERCENT (PWM_25KHZ_PERIOD - 0x64)
//#define DUTYCYCLE_50_PERCENT (PWM_25KHZ_PERIOD - 0x3e9)
//#define DUTYCYCLE_75_PERCENT (PWM_25KHZ_PERIOD - 0x5DD)

#define CONTROL_SET_CURRENT 0
#define CONTROL_SET_SPEED 1
#define CONTROL_SET_POSITION 2
#define CONTROL_SET_TORQUE 3

#define MOTOR_VOLTAGE 24
#define MAX_VOLTAGE 12
#define MIN_VOLTAGE -12
#define MAX_PWM 50		/* MAX PWM Duty Cycle */
#define MIN_PWM -50		/* MAX REVERSE PWM DUTY CYCLE */
#define MAX_POS 140		/* MAX Joint Position in Degrees*/
#define MIN_POS 0		/* MIN Joint Position in Degrees*/
#define MAX_TORQUE 4	/* MAX Torque Value in Nm*/
#define MIN_TORQUE -4	/* MIN Torque Value in Nm*/



/************************************************************************/
/* Global Variables                                                     */
/************************************************************************/

volatile static int current_button_controlled_dutycycle_state = 0;
volatile static uint32_t current_BLDC_commutation_state = 0;
volatile static int last_BLDC_commutation_state = -1;
volatile static int8_t current_BLDC_direction = 0;
volatile static uint8_t current_BLDC_dutycycle = 0;
volatile static int32_t BLDC_revolutions = 0;
volatile static float BLDC_relative_steps = 0;
//volatile static int32_t current_BLDC_motor_rpm=0;



/* Pattern Buffer Settings for the 6 commutations states*/
/* State0, State1, State2, State3, State4, State5*/	
static uint16_t BLDC_commutation_clockwise[] = {0x082D, 0x202D, 0x2036, 0x1036, 0x101B, 0x081B};
static uint16_t BLDC_commutation_counter_clockwise[] = {0x1036, 0x101B, 0x081B, 0x082D, 0x202D, 0x2036};

/*EXplained Pro Board Pattern Buffer*/
// static uint16_t BLDC_commutation_clockwise[] = {0x507C, 0x607C, 0x30F4, 0x50F4, 0x60F8, 0x30F8};
// static uint16_t BLDC_commutation_counter_clockwise[] = {0x50F4, 0x60F8, 0x30F8, 0x507C, 0x607C, 0x30F4};



/* Current Measurements */
extern volatile uint16_t ADC_IB_value;
extern volatile uint16_t ADC_IC_value;
extern volatile float currentC_value;
extern volatile float currentB_value;
extern volatile float current_reference_current_value;
extern volatile float last_reference_current_value;
extern volatile uint8_t new_current_value_available_flag;

/* Speed Measurements */
extern volatile float current_BLDC_motor_rpm;
extern volatile uint16_t CC0_value ;
extern volatile uint16_t CC1_value ;
extern volatile uint8_t new_speed_value_available_flag;

/* Position Measurements */
extern volatile float encoder_joint_pos;
extern unsigned int encoder_joint_warning_bit;
extern unsigned int encoder_joint_error_bit;
extern volatile char encoder_spi_reply[7];
extern volatile int new_encoder_reading_flag ;
extern volatile int read_encoder_flag;

extern volatile float joint_torque;

/*controller values*/
extern volatile float error_current;
extern volatile float error_speed;
extern volatile float error_position;
extern volatile float control_voltage_output;
extern volatile float current_control_output[4];		//Output - prev. Output - prev. error - not used
extern volatile float speed_control_output[4];		//Output - prev. Output - prev. error - not used
extern volatile float position_control_output[4];		//Output - prev. Output - prev. error - not used

//general
extern volatile uint16_t input_control_mode;		//turn on/off controller
extern volatile uint16_t input_control_set;		//select between inputs

//current control
extern volatile float input_desired_current;		//target current
extern volatile float input_max_current;			//max possible current
extern volatile float input_min_current;			//max negative current
extern volatile float input_kp_current;			//p gain current control
extern volatile float input_ki_current;			//i gain current control

//speed control
extern volatile float input_desired_speed;			//target speed
extern volatile float input_speed_max;		//max possible motor speed
extern volatile float input_speed_min;		//max negative motor speed
extern volatile float input_kp_speed_control;		//p gain position control
extern volatile float input_ki_speed_control;		//p gain position control

//position control
extern volatile float input_desired_position;		//target position
extern volatile float input_max_position;			// max position
extern volatile float input_min_position;			// max neg. position
extern volatile float input_kp_position_control;	//p gain position control
extern volatile float input_ki_position_control;

PIDvariable currentPIDVar;
PIDcontrol currentPIDControl;
PIDvariable speedPIDVar;
PIDcontrol speedPIDControl;
PIDvariable posPIDVar;
PIDcontrol posPIDControl;
PIDvariable torquePIDVar;
PIDcontrol torquePIDControl;

//feedforward voltage control
extern volatile float input_kt_feedforward;

/************************************************************************/
/* Functions                                                            */
/************************************************************************/

/* Init Functions */
void init_PWM();
void init_currentPID();
void init_speedPID();
void init_posPID();
void init_posPID();

/*Button controlled functions*/
void check_sw0_pressed();
void button_controlled_dutycycle_state_machine();

/*General BLDC functions*/
int set_PWM_dutycycle(float dutycycle);
void BLDC_find_step();
void BLDC_revolution_counter();
void BLDC_drive(float DirectionAndDutycycle);

void BLDC_control_current();
void BLDC_control_speed();
void BLDC_control_position();

/*Get functions*/
uint32_t get_BLDC_commutation_state();
float get_BLDC_relative_steps();
uint16_t get_BLDC_revolutions();
int8_t get_BLDC_direction();

#endif /* BLDC_DRIVER_H_ */

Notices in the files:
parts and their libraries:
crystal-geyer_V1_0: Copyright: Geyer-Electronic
